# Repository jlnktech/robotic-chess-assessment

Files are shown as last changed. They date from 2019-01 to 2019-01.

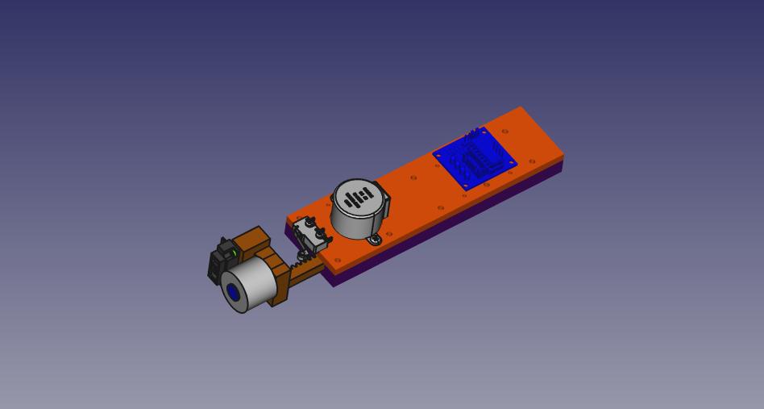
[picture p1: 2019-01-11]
cad/images/image.jpg

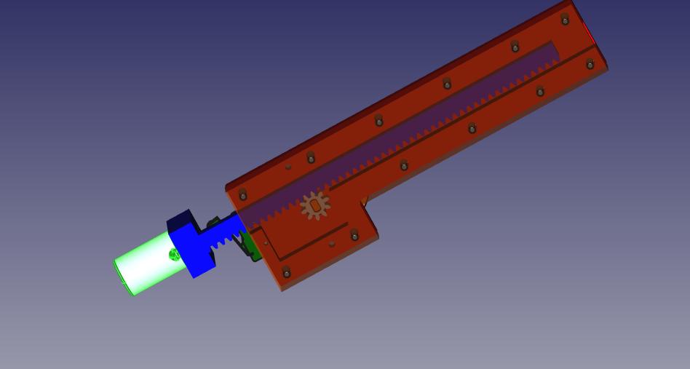
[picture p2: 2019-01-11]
cad/images/image1.jpg

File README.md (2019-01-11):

# robotic-chess-assessment
low cost chess robot

kicad folder contains schematic layout of hall effect detection using DRV5053. Idea is to scan 8 squares (1 row) at once, then repeat for other 7 rows to cut down on time. Each piece must have magnet attached.

pcb123 folder contains schematic layout of IR sensors using QRE1113. Once again, scan 1 row (8 squares) then repeat. Each piece must have reflect material on the bottom and be able to cover the slot on each of the squares.

CAD folder contains the mechanical layout of the xyz table

firmware folder contains arduino test for the z-axis portion

yet to be done is to add the raspberry pi actual chess code

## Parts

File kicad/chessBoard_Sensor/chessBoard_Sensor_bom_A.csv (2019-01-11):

Component | Description | Part | References | Value | Footprint | Quantity Per PCB | Datasheet | Field4 | Category | Status | Family | MPN | Digi-Key_PN | DK_Datasheet_Link | DK_Detail_Page | Manufacturer
1 | 0.1uF ceramic capacitors A capacitor is a passive two-terminal electrical component used to store electrical energy temporarily in an electric field. | 0.1UF-0402-16V-10% | C1 C2 C3 C4 C5 C6 C7 C8 C9 C10 C11 C12 C13 C14 C15 C16 C17 C18 C19 C20 C21 C22 C23 C24 C25 C26 C27 C28 C29 C30 C31 C32 C33 C34 C35 C36 C37 C38 C39 C40 C41 C42 C43 C44 C45 C46 C47 C48 C49 C50 C51 C52 C53 C54 C55 C56 C57 C58 C59 C60 C61 C62 C63 C64 C65 C66 C67 C68 C69 C70 C71 C72 C73 | 0.1UF-0402-16V-10% | 0402 | 73 |  | CAP-12416
2 |  | HEADER_6 | J1 | HEADER_6 | JST_PH_S6B-PH-SM4-TB_1x06-1MP_P2.00mm_Horizontal | 1
3 | Resistor | R | R1 R2 R3 R4 R5 R6 R7 R8 R9 R10 R11 R12 R13 R14 R15 R16 R17 R18 R19 | 10K, 5%, 402 | R_0402_1005Metric | 19 | ~
4 | 3x DIP Switch, Single Pole Single Throw (SPST) switch, small symbol | SW_DIP_x03 | SW1 | SW_DIP_x03 | SW_DIP_SPSTx03_Slide_6.7x9.18mm_W8.61mm_P2.54mm_LowProfile | 1
5 | 12-Bit, 8-Channel, ADC System Monitor With Temperature Sensor, I2C Interface, TSSOP-16 | ADC128D818 | U9 U18 U27 U36 U45 U54 U63 U72 | ADC128D818 | TSSOP-16_4.4x5mm_P0.65mm | 8 | http://www.ti.com/lit/ds/symlink/adc128d818.pdf
6 | SENSOR LINEAR ANALOG SOT23-3 | DRV5053VAQDBZR | U1 U2 U3 U4 U5 U6 U7 U8 U10 U11 U12 U13 U14 U15 U16 U17 U19 U20 U21 U22 U23 U24 U25 U26 U28 U29 U30 U31 U32 U33 U34 U35 U37 U38 U39 U40 U41 U42 U43 U44 U46 U47 U48 U49 U50 U51 U52 U53 U55 U56 U57 U58 U59 U60 U61 U62 U64 U65 U66 U67 U68 U69 U70 U71 | DRV5053VAQDBZR | sot323 | 64 | http://www.ti.com/lit/ds/symlink/drv5053.pdf |  | Sensors, Transducers | Active | Magnetic Sensors - Linear, Compass (ICs) | DRV5053VAQDBZR | 296-38460-1-ND | http://www.ti.com/lit/ds/symlink/drv5053.pdf | /product-detail/en/texas-instruments/DRV5053VAQDBZR/296-38460-1-ND/5022225 | Texas Instruments
7 | 4-channel I2C-bus multiplexer with interrupt logic, TSSOP20 package | PCA9544APW | U73 | PCA9544APW | TSSOP-20_4.4x6.5mm_P0.65mm | 1 | http://www.nxp.com/documents/data_sheet/PCA9544A.pdf
Component Groups: | 7
Component Count: | 167
Fitted Components: | 167
Number of PCBs: | 1
Total components: | 167
Schematic Version: | A
Schematic Date: | 2019-01-01
BoM Date: | Fri 04 Jan 2019 08:12:23 PM PST
Schematic Source: | /home/jlnktech/workspace/kicad_projects/chessBoard_Sensor/chessBoard_Sensor.sch
KiCad Version: | Eeschema 6.0.0-rc1-unknown-62e2fe8~66~ubuntu18.04.1

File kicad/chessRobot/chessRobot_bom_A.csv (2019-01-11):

Component | Description | Part | References | Value | Footprint | Quantity Per PCB | Datasheet | Field4 | Category | Status | Family | MPN | Digi-Key_PN | DK_Datasheet_Link | DK_Detail_Page | Manufacturer
1 | 1uF ceramic capacitors A capacitor is a passive two-terminal electrical component used to store electrical energy temporarily in an electric field. | 1.0UF-0805-25V-10% | C1 | 1.0UF, 25V | 0805 | 1
2 | 47uF polarized capacitors A capacitor is a passive two-terminal electrical component used to store electrical energy temporarily in an electric field. | 47UF-POLAR-EIA3528-10V-10% | C2 C3 | 47UF, 10V | EIA3528 | 2 |  | CAP-08310
3 | 50V 1A General Purpose Rectifier Diode, DO-41 | 1N4001 | D1 D2 | 1N4001 | D_DO-41_SOD81_P10.16mm_Horizontal | 2 | http://www.vishay.com/docs/88503/1n4001.pdf
4 | Generic connector, double row, 02x05, odd/even pin numbering scheme (row 1 odd numbers, row 2 even numbers), script generated (kicad-library-utils/schlib/autogen/connector/) | Conn_02x05_Odd_Even | J1 | 0430201001 |  | 1 | https://www.molex.com/pdm_docs/sd/430201001_sd.pdf
5 | Multi connection point. Often used as Generic Header-pin footprint for 0.1 inch spaced/style header connections <b>On any of the 0.1 inch spaced packages, you can populate with these:</b><ul><li><a href="https://www.sparkfun.com/products/116"> Break Away Headers - Straight</a> (PRT-00116)</li><li><a href="https://www.sparkfun.com/products/553"> Break Away Male Headers - Right Angle</a> (PRT-00553)</li><li><a href="https://www.sparkfun.com/products/115"> Female Headers</a> (PRT-00115)</li><li><a href="https://www.sparkfun.com/products/117"> Break Away Headers - Machine Pin</a> (PRT-00117)</li><li><a href="https://www.sparkfun.com/products/743"> Break Away Female Headers - Swiss Machine Pin</a> (PRT-00743)</li></ul><b> For SCREWTERMINALS and SPRING TERMINALS visit here:</b><ul><li><a href="https://www.sparkfun.com/search/results?term=Screw+Terminals"> Screw Terimnals on SparkFun.com</a> (5mm/3.5mm/2.54mm spacing)</li></ul><b>This device is also useful as a general connection point to wire up your design to another part of your project. Our various solder wires solder well into these plated through hole pads.</b><ul><li><a href="https://www.sparkfun.com/products/11375"> Hook-Up Wire - Assortment (Stranded, 22 AWG)</a> (PRT-11375)</li><li><a href="https://www.sparkfun.com/products/11367"> Hook-Up Wire - Assortment (Solid Core, 22 AWG)</a> (PRT-11367)</li><li><a href="https://www.sparkfun.com/categories/141"> View the entire wire category on our website here</a></li></ul><b>Special notes:</b> Molex polarized connector foot print use with SKU : PRT-08231 with associated crimp pins and housings. 1MM SMD Version SKU: PRT-10208 | CONN_05JST-VERT | J3 | CONN_05JST-VERT | JST-5-PTH-VERT | 1 |  | XXX-00000
6 | Multi connection point. Often used as Generic Header-pin footprint for 0.1 inch spaced/style header connections <b>On any of the 0.1 inch spaced packages, you can populate with these:</b><ul><li><a href="https://www.sparkfun.com/products/116"> Break Away Headers - Straight</a> (PRT-00116)</li><li><a href="https://www.sparkfun.com/products/553"> Break Away Male Headers - Right Angle</a> (PRT-00553)</li><li><a href="https://www.sparkfun.com/products/115"> Female Headers</a> (PRT-00115)</li><li><a href="https://www.sparkfun.com/products/117"> Break Away Headers - Machine Pin</a> (PRT-00117)</li><li><a href="https://www.sparkfun.com/products/743"> Break Away Female Headers - Swiss Machine Pin</a> (PRT-00743)</li></ul><b> For SCREWTERMINALS and SPRING TERMINALS visit here:</b><ul><li><a href="https://www.sparkfun.com/search/results?term=Screw+Terminals"> Screw Terimnals on SparkFun.com</a> (5mm/3.5mm/2.54mm spacing)</li></ul><b>This device is also useful as a general connection point to wire up your design to another part of your project. Our various solder wires solder well into these plated through hole pads.</b><ul><li><a href="https://www.sparkfun.com/products/11375"> Hook-Up Wire - Assortment (Stranded, 22 AWG)</a> (PRT-11375)</li><li><a href="https://www.sparkfun.com/products/11367"> Hook-Up Wire - Assortment (Solid Core, 22 AWG)</a> (PRT-11367)</li><li><a href="https://www.sparkfun.com/categories/141"> View the entire wire category on our website here</a></li></ul><b>Special notes:</b> Molex polarized connector foot print use with SKU : PRT-08231 with associated crimp pins and housings. 1MM SMD Version SKU: PRT-10208 | CONN_05JST-VERT | J2 | JST B5B | B5B-XH-A(LF)(SN) | 1 | http://www.jst-mfg.com/product/pdf/eng/eXH.pdf | XXX-00000
7 | Generic screw terminal, single row, 01x02, script generated (kicad-library-utils/schlib/autogen/connector/) | Screw_Terminal_01x02 | J4 J6 | Screw_Terminal_01x02 |  | 2 | ~
8 | Generic screw terminal, single row, 01x03, script generated (kicad-library-utils/schlib/autogen/connector/) | Screw_Terminal_01x03 | J5 | Screw_Terminal_01x03 |  | 1 | ~
9 | 5-wire unipolar stepper motor | Stepper_Motor_unipolar_5pin | M1 | 858 |  | 1 | https://media.digikey.com/pdf/Data%20Sheets/Adafruit%20PDFs/858_Web.pdf
10 | P-channel MOSFETs Voltage controlled devices that allow control of high current outputs. <b>SparkFun Products:</b><ul><li><a href= https://www.sparkfun.com/products/13907 >SparkFun ESP32 Thing</a></li><li><a href= https://www.sparkfun.com/products/13231 >SparkFun ESP8266 Thing</a></li></ul> | MOSFET_PCH-SI2309DS | Q2 | LR120 | d2-pak | 1
11 | Generic Resistor Package | RESISTOR0603 | R2 | 100, 5% | 0603 | 1
12 | Generic Resistor Package | RESISTOR0603 | R1 | 10K, 5% | 0603 | 1
13 | IC PWR RELAY 7NPN 1:1 16DIP | ULN2003AN | U1 | ULN2003AN | DIP-16_W7.62mm | 1 | http://www.ti.com/lit/ds/symlink/uln2003a.pdf |  | Discrete Semiconductor Products | Active | Transistors - Bipolar (BJT) - Arrays | ULN2003AN | 296-1979-5-ND | http://www.ti.com/lit/ds/symlink/uln2003a.pdf | /product-detail/en/texas-instruments/ULN2003AN/296-1979-5-ND/277624 | Texas Instruments
Component Groups: | 13
Component Count: | 16
Fitted Components: | 16
Number of PCBs: | 1
Total components: | 16
Schematic Version: | A
Schematic Date: | 2019-01-07
BoM Date: | Tue 08 Jan 2019 07:28:10 AM PST
Schematic Source: | /home/jlnktech/workspace/kicad_projects/chessRobot/chessRobot.sch
KiCad Version: | Eeschema 6.0.0-rc1-unknown-62e2fe8~66~ubuntu18.04.1

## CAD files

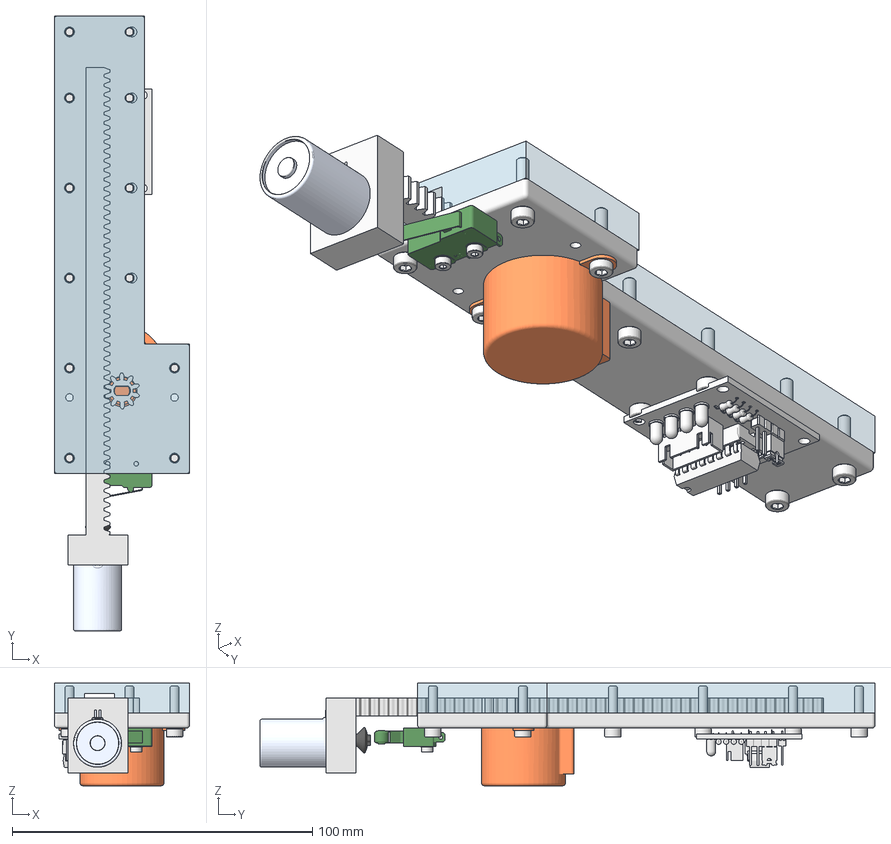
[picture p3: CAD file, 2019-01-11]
cad/assembly.fcstd
45.0 x 204.9 x 34.2 mm
M3x14-Screw002
M3x14-Screw013
M3x14-Screw014
M3x14-Screw016
M3x14-Screw015
M3x14-Screw008
M3x14-Screw009
M3x14-Screw010
M3x14-Screw011
M3x14-Screw012
M3x14-Screw017
M3x14-Screw
M2x10-Screw
M2x10-Screw001
28byj-48
Microswitch
M4x12-Screw
wf-p10-25_electro
basePlate
rack
gear
coverPlate
ULN2003Board

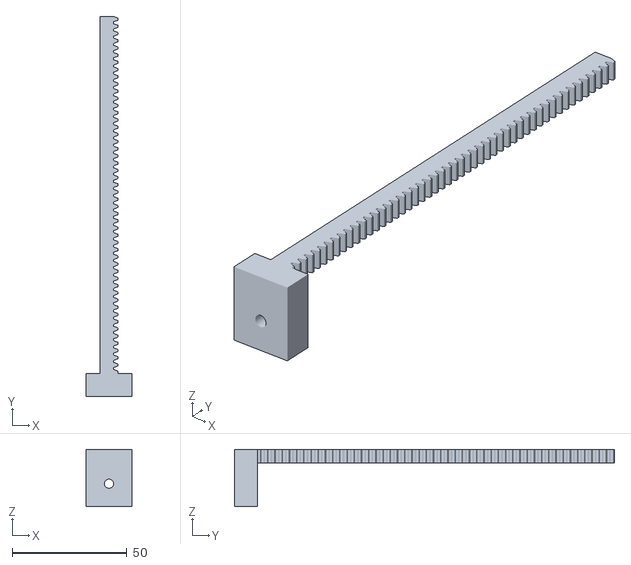
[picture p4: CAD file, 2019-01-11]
cad/3dPrinterFiles/rack.STL
20.0 x 165.7 x 25.0

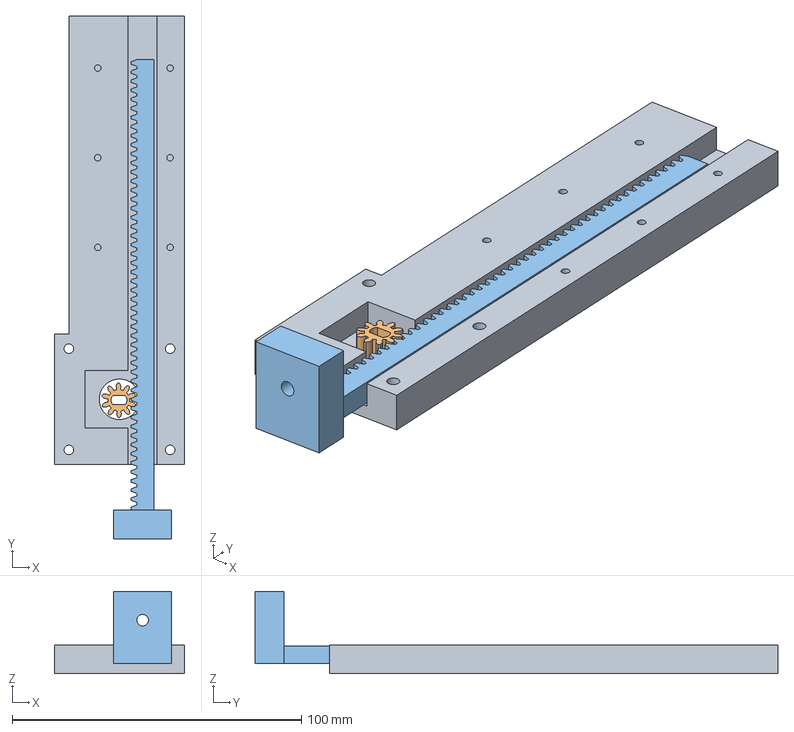
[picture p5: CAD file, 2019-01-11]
cad/new_cover.fcstd
45.0 x 180.8 x 28.5 mm
cover
gear
rack

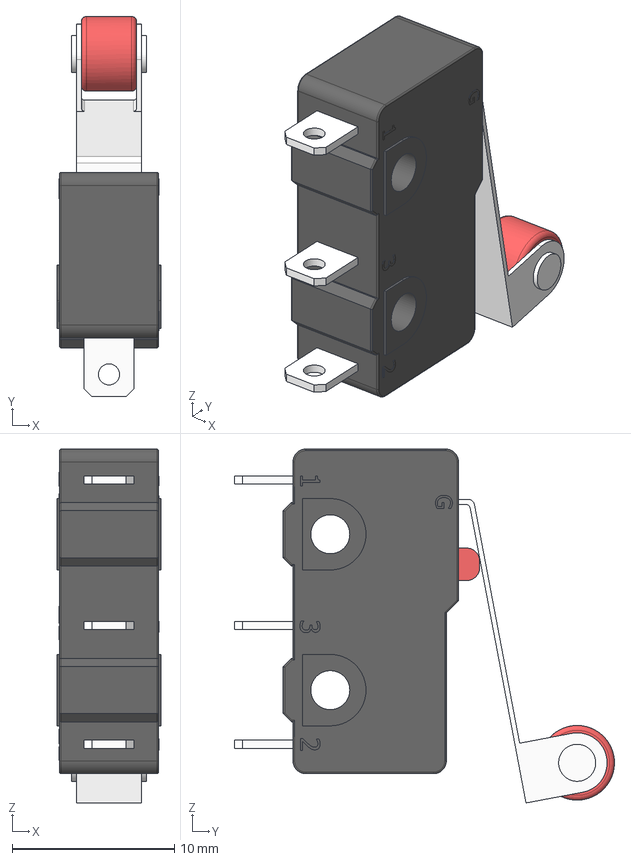
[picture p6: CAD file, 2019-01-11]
cad/support/Microswitch.stp
6.40 x 23.4 x 21.8 mm

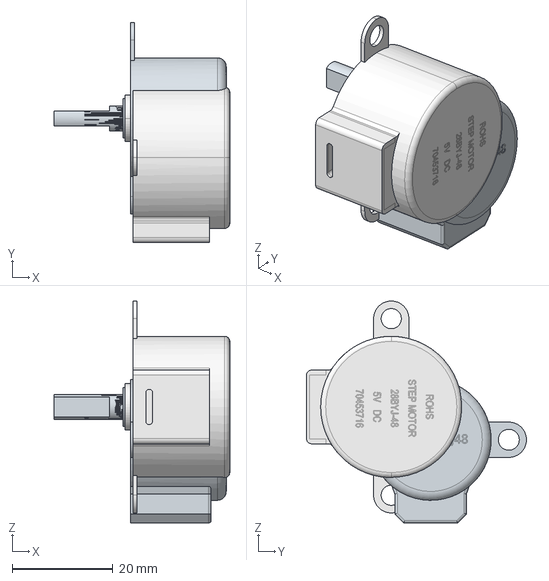
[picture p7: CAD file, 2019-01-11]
cad/tests/motor_combo.fcstd
34.8 x 43.6 x 44.0 mm
5V DC STEP MOTOR

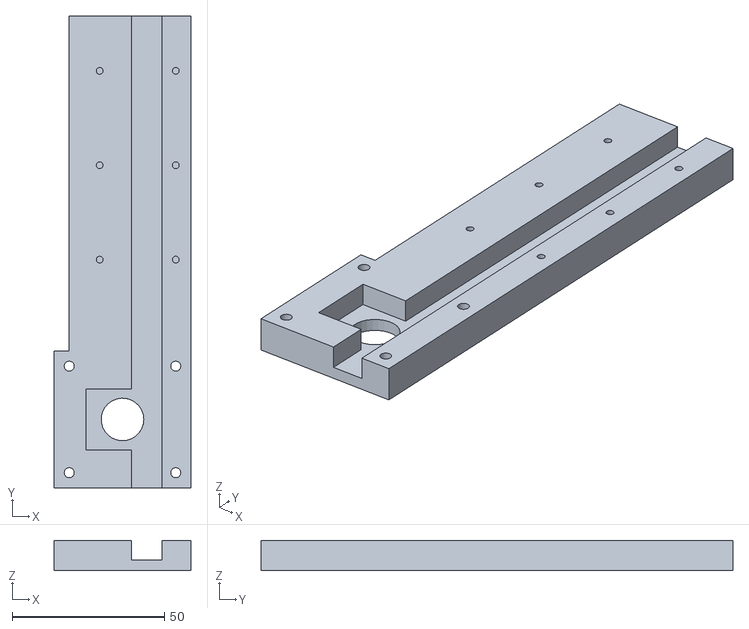
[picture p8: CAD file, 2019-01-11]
cad/3dPrinterFiles/newCover.stl
45.0 x 155.0 x 10.0

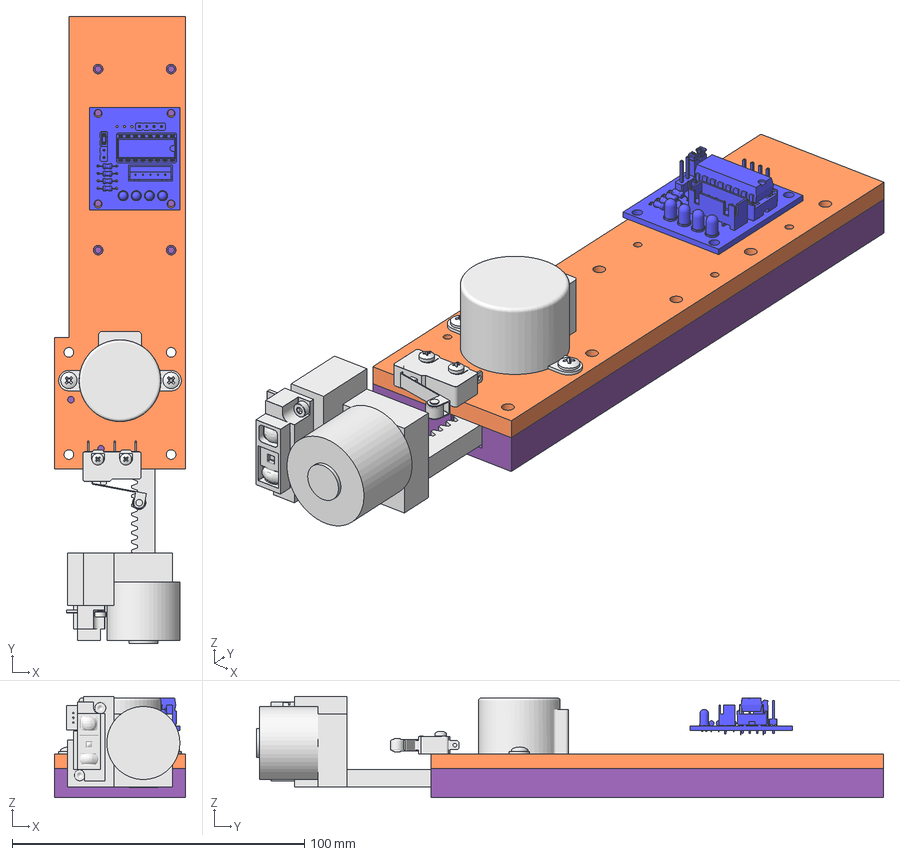
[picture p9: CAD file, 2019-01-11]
cad/new_base_cover.fcstd
45.0 x 214.7 x 34.7 mm
M3x5-Screw
M3x5-Screw001
M2x10-Screw
M2x10-Screw001
Microswitch 20mm
28BYJ-48
newRack
gear
ULN2003Board
newCover
newBase

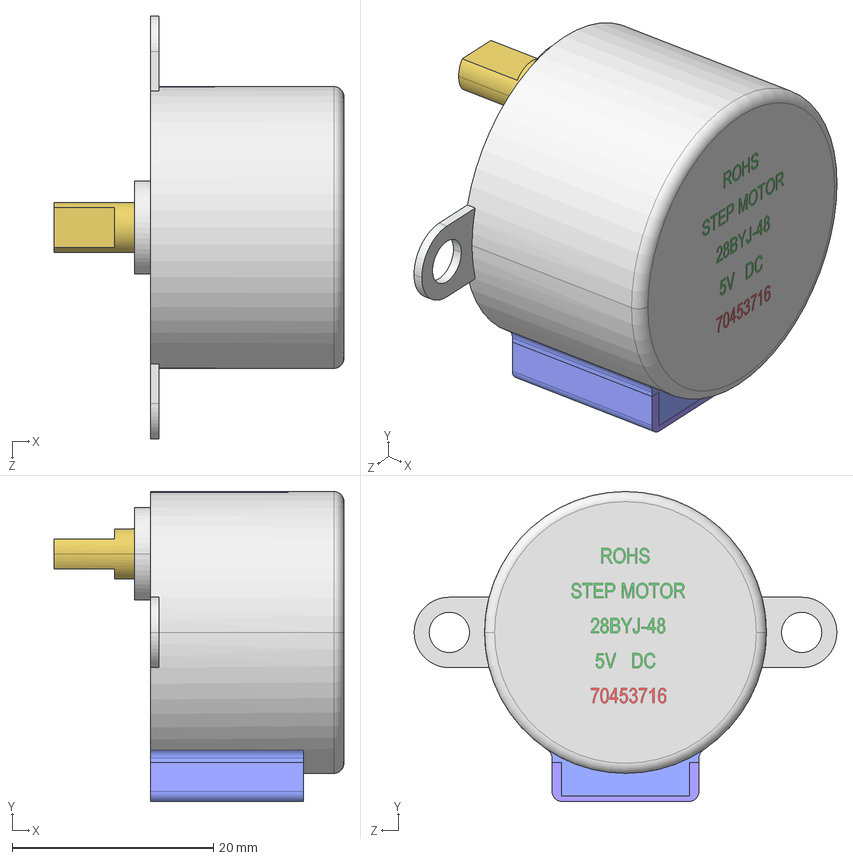
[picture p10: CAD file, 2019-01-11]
cad/support/28byj-48.stp
28.8 x 30.8 x 42.0 mm

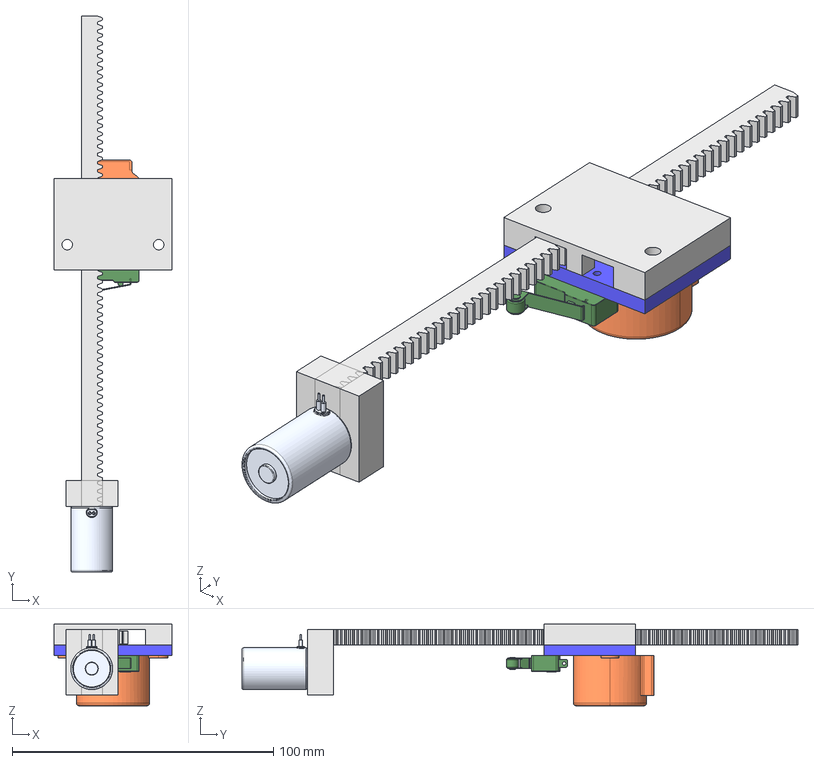
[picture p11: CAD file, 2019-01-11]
cad/tests/stepper_motion_backup.fcstd
45.0 x 212.7 x 31.2 mm
28byj-48
Microswitch 20mm
newGear
wf-p10-25_electro
newRack
newBase
newCover

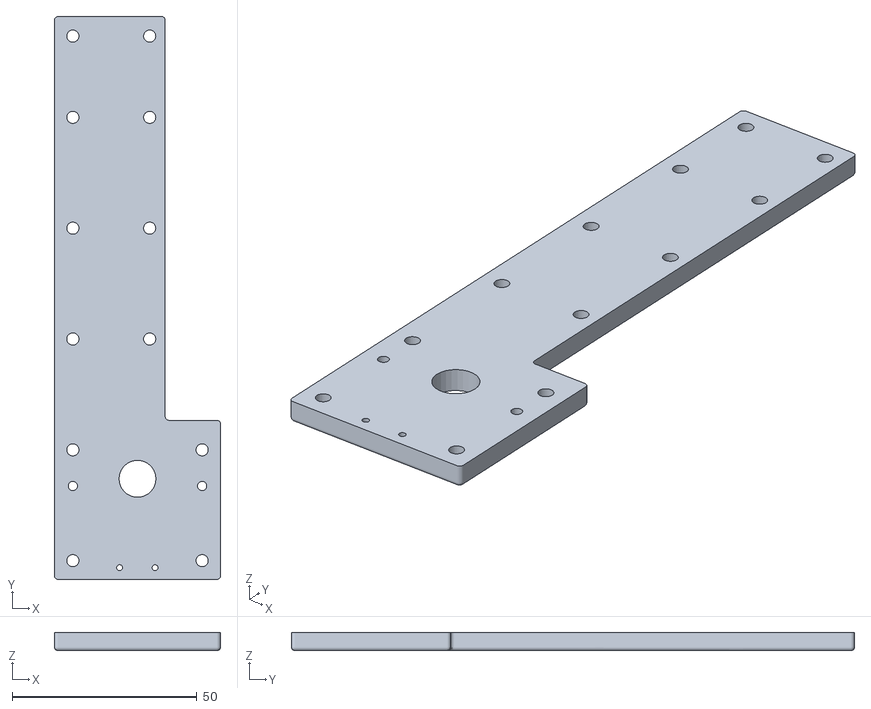
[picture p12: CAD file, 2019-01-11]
cad/3dPrinterFiles/base.stl
45.0 x 152.4 x 5.00

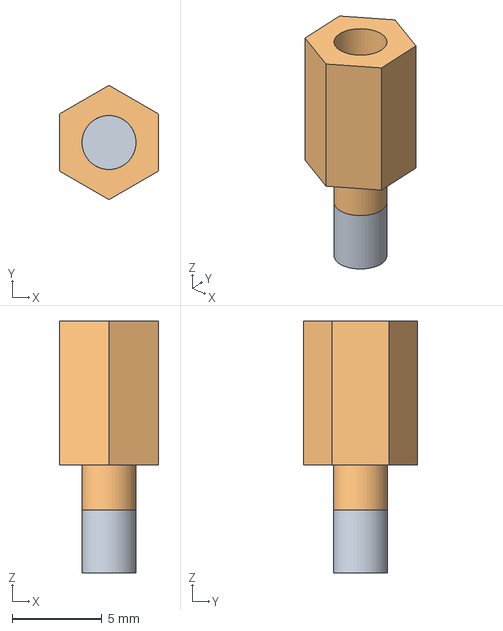
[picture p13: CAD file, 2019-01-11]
cad/support/standoff_m3.fcstd
5.50 x 6.35 x 14.0 mm

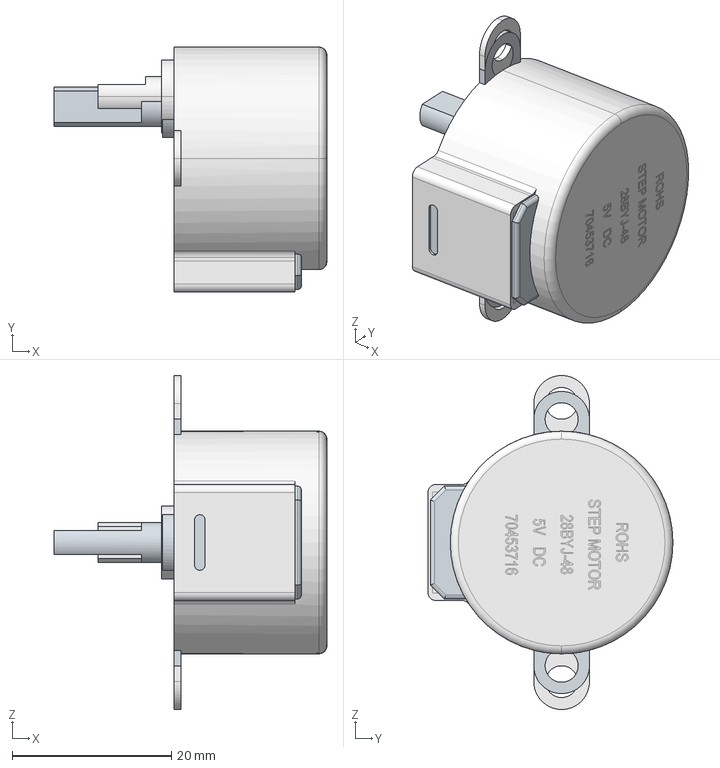
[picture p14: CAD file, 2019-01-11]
cad/tests/measurement_two_motors.fcstd
34.3 x 30.8 x 42.0 mm
28BYJ-48
24BYJ-48

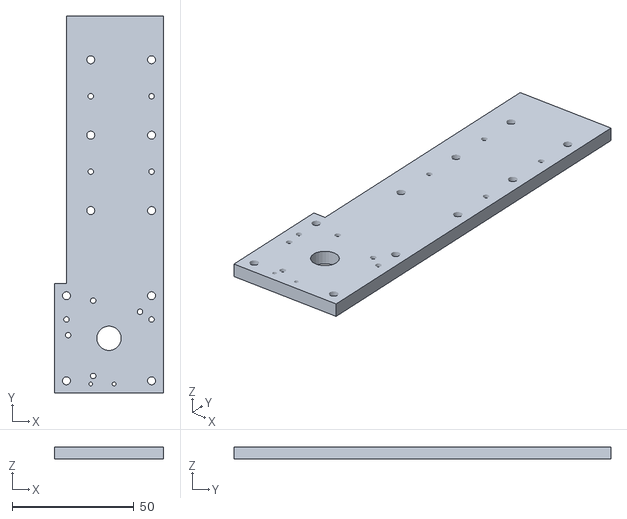
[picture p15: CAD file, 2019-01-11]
cad/3dPrinterFiles/newBase.stl
45.0 x 155.0 x 5.00

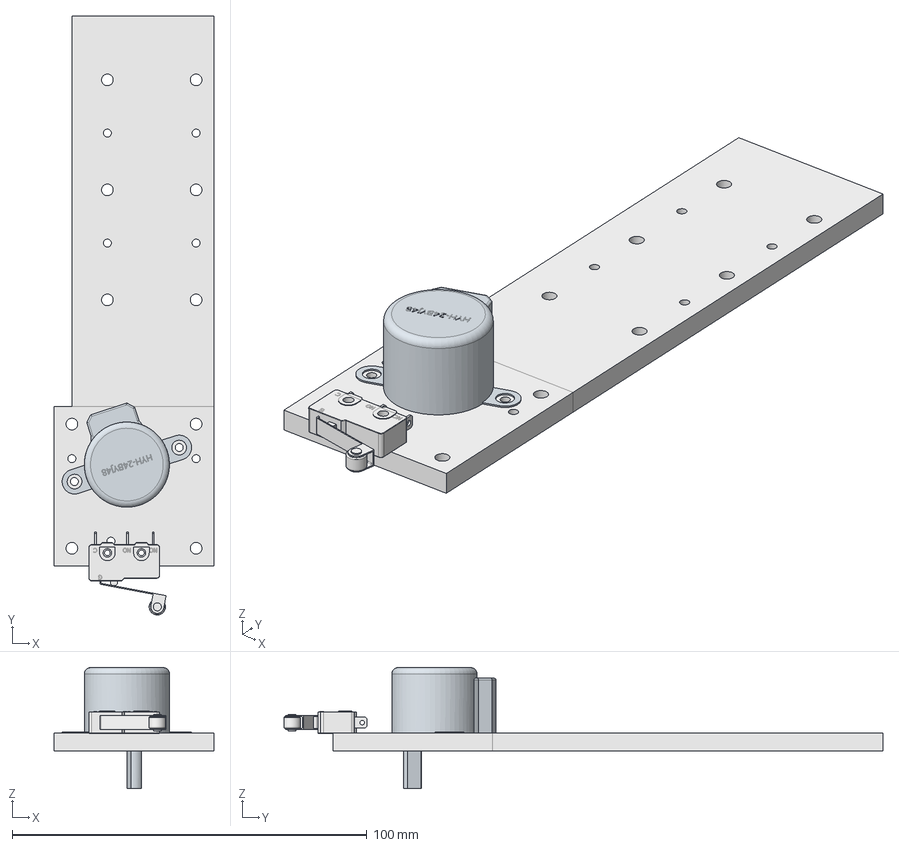
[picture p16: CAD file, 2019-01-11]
cad/new_base.fcstd
45.0 x 168.8 x 34.2 mm
48BYJ-48
Microswitch 20mm
Base

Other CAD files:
cad/support/WF-p25_20.FCStd
cad/tests/stepper_motion.fcstd
cad/3dPrinterFiles/motor_combo.stl
cad/new_rack.FCStd
cad/3dPrinterFiles/cover.stl
cad/3dPrinterFiles/gear.stl
cad/3dPrinterFiles/newRack.stl
cad/old/base.fcstd
cad/old/cover.fcstd
cad/old/gear.fcstd
cad/old/rack.fcstd
cad/support/GP2Y0A51SK0F.FCStd
cad/support/ULN2003Board.stl
cad/support/ULN2003_board.fcstd
cad/support/hyh-24byj48.step
cad/support/sot23-3.fcstd
cad/support/standoff_m3.stl

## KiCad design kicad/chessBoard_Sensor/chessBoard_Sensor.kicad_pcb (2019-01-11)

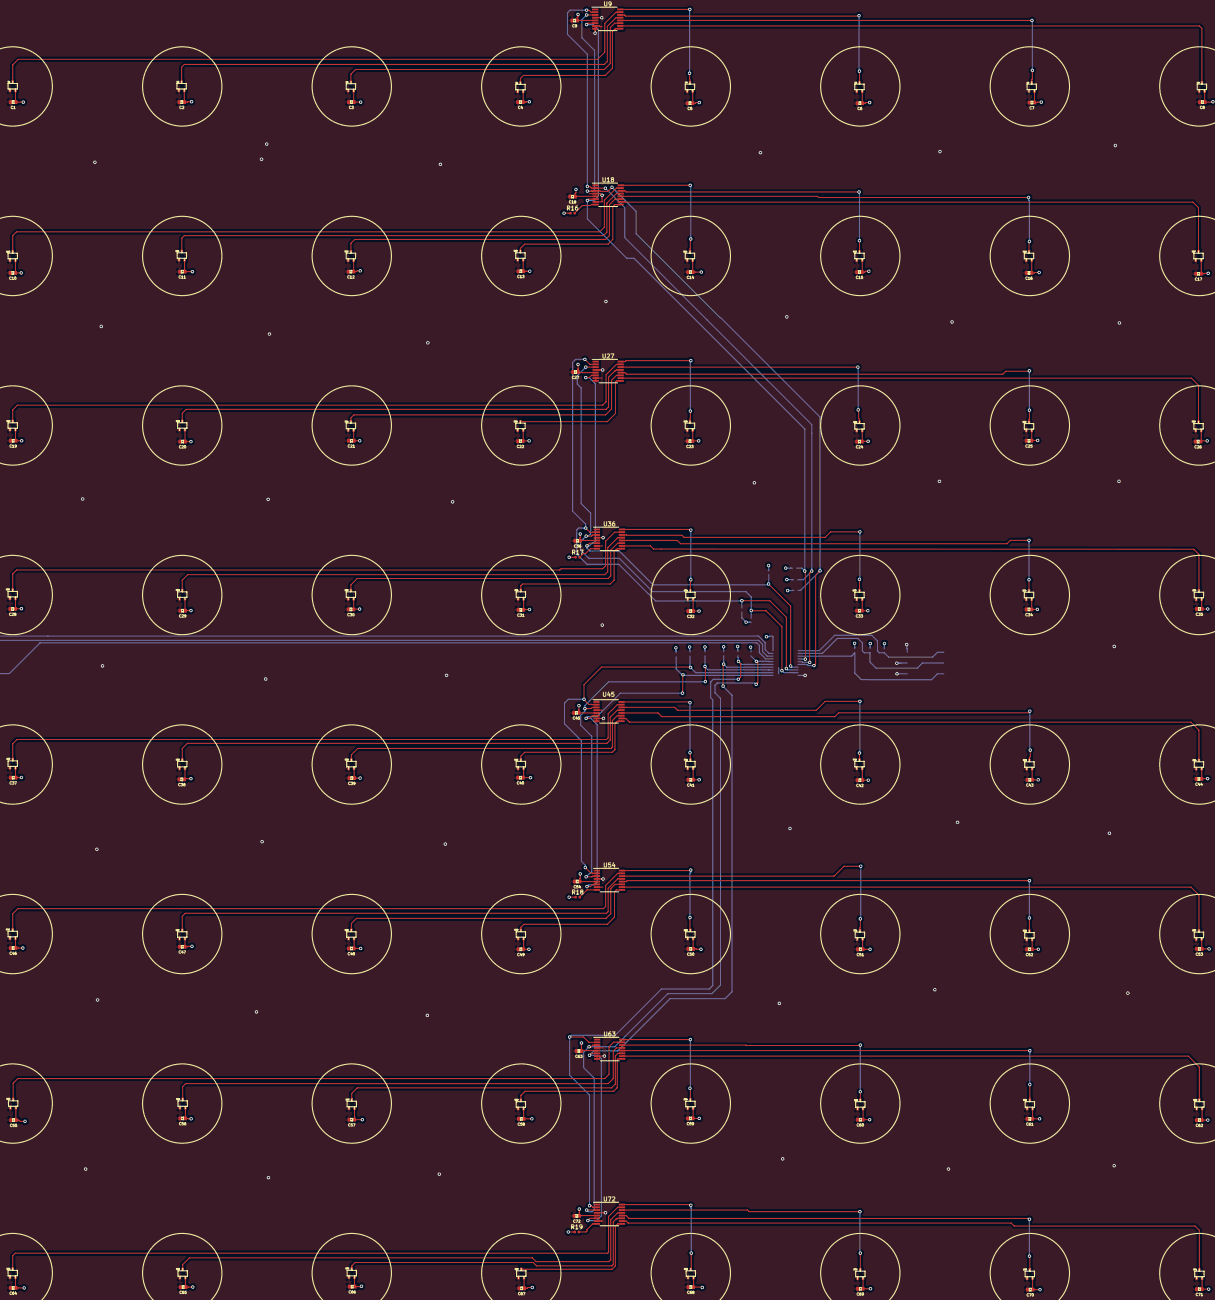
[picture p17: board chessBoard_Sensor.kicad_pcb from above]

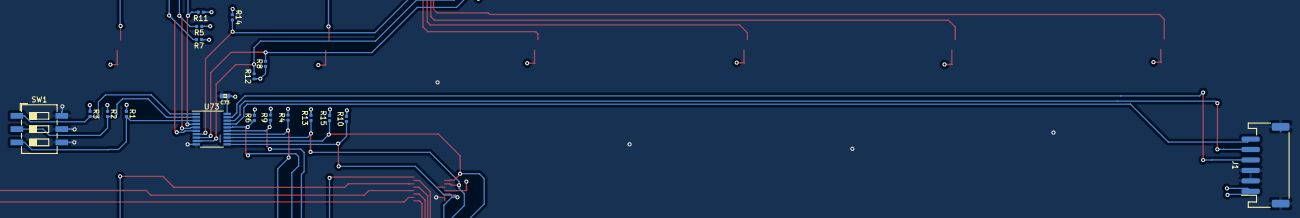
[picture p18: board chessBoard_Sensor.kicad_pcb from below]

Board: 4 copper layers, 167 parts (19 on the bottom side), 88 nets.

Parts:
C1, C2, C3, C4, C5, C6, C7, C8, C9, C10, C11, C12, C13, C14, C15, C16, C17, C18, C19, C20, C21, C22, C23, C24, C25, C26, C27, C28, C29, C30, C31, C32, C33, C34, C35, C36, C37, C38, C39, C40, C41, C42, C43, C44, C45, C46, C47, C48, C49, C50, C51, C52, C53, C54, C55, C56, C57, C58, C59, C60, C61, C62, C63, C64, C65, C66, C67, C68, C69, C70, C71, C72, C73: 0.1UF-0402-16V-10%; 0402
J1: HEADER_6; JST_PH_S6B-PH-SM4-TB_1x06-1MP_P2.00mm_Horizontal
R1, R2, R3, R4, R5, R6, R7, R8, R9, R10, R11, R12, R13, R14, R15, R16, R17, R18, R19: 10K, 5%, 402; R_0402_1005Metric
SW1: SW_DIP_x03; SW_DIP_SPSTx03_Slide_6.7x9.18mm_W8.61mm_P2.54mm_LowProfile
U1, U2, U3, U4, U5, U6, U7, U8, U10, U11, U12, U13, U14, U15, U16, U17, U19, U20, U21, U22, U23, U24, U25, U26, U28, U29, U30, U31, U32, U33, U34, U35, U37, U38, U39, U40, U41, U42, U43, U44, U46, U47, U48, U49, U50, U51, U52, U53, U55, U56, U57, U58, U59, U60, U61, U62, U64, U65, U66, U67, U68, U69, U70, U71: DRV5053VAQDBZR; sot323
U9, U18, U27, U36, U45, U54, U63, U72: ADC128D818; TSSOP-16_4.4x5mm_P0.65mm
U73: PCA9544APW; TSSOP-20_4.4x6.5mm_P0.65mm

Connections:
+3V3: C1.1, C2.1, C3.1, C4.1, C5.1, C6.1, C7.1, C8.1, C9.1, C10.1, C11.1, C12.1, C13.1, C14.1, C15.1, C16.1, C17.1, C18.1, C19.1, C20.1, C21.1, C22.1, C23.1, C24.1, C25.1, C26.1, C27.1, C28.1, C29.1, C30.1, C31.1, C32.1, C33.1, C34.1, C35.1, C36.1, C37.1, C38.1, C39.1, C40.1, C41.1, C42.1, C43.1, C44.1, C45.1, C46.1, C47.1, C48.1, C49.1, C50.1, C51.1, C52.1, C53.1, C54.1, C55.1, C56.1, C57.1, C58.1, C59.1, C60.1, C61.1, C62.1, C63.1, C64.1, C65.1, C66.1, C67.1, C68.1, C69.1, C70.1, C71.1, C72.1, C73.1, J1.1, R1.1, R2.1, R3.1, R4.2, R5.1, R6.2, R7.1, R8.1, R9.2, R10.2, R11.1, R12.1, R13.2, R14.1, R15.2, R16.1, R17.1, R18.1, R19.1, U1.3, U2.3, U3.3, U4.3, U5.3, U6.3, U7.3, U8.3, U9.5, U10.3, U11.3, U12.3, U13.3, U14.3, U15.3, U16.3, U17.3, U18.5, U19.3, U20.3, U21.3, U22.3, U23.3, U24.3, U25.3, U26.3, U27.5, U28.3, U29.3, U30.3, U31.3, U32.3, U33.3, U34.3, U35.3, U36.5, U37.3, U38.3, U39.3, U40.3, U41.3, U42.3, U43.3, U44.3, U45.5, U46.3, U47.3, U48.3, U49.3, U50.3, U51.3, U52.3, U53.3, U54.5, U55.3, U56.3, U57.3, U58.3, U59.3, U60.3, U61.3, U62.3, U63.5, U64.3, U65.3, U66.3, U67.3, U68.3, U69.3, U70.3, U71.3, U72.5, U73.20
/Sheet1/INT1: R11.2, U9.6, U18.6, U73.4
/Sheet1/SCL1: R7.2, U9.3, U18.3, U73.6
/Sheet1/SDA1: R5.2, U9.2, U18.2, U73.5
/sheet5C2B8B4A/INT4: R4.1, U63.6, U72.6, U73.14
/sheet5C2B8B4A/SCL4: R6.1, U63.3, U72.3, U73.16
/sheet5C2B8B4A/SDA4: R9.1, U63.2, U72.2, U73.15
/sheet5C2B89C0/INT3: R10.1, U45.6, U54.6, U73.11
/sheet5C2B89C0/SCL3: R13.1, U45.3, U54.3, U73.13
/sheet5C2B89C0/SDA3: R15.1, U45.2, U54.2, U73.12
/sheet5C2B878C/INT2: R14.2, U27.6, U36.6, U73.7
/sheet5C2B878C/SCL2: R12.2, U27.3, U36.3, U73.9
/sheet5C2B878C/SDA2: R8.2, U27.2, U36.2, U73.8
GND: C1.2, C2.2, C3.2, C4.2, C5.2, C6.2, C7.2, C8.2, C9.2, C10.2, C11.2, C12.2, C13.2, C14.2, C15.2, C16.2, C17.2, C18.2, C19.2, C20.2, C21.2, C22.2, C23.2, C24.2, C25.2, C26.2, C27.2, C28.2, C29.2, C30.2, C31.2, C32.2, C33.2, C34.2, C35.2, C36.2, C37.2, C38.2, C39.2, C40.2, C41.2, C42.2, C43.2, C44.2, C45.2, C46.2, C47.2, C48.2, C49.2, C50.2, C51.2, C52.2, C53.2, C54.2, C55.2, C56.2, C57.2, C58.2, C59.2, C60.2, C61.2, C62.2, C63.2, C64.2, C65.2, C66.2, C67.2, C68.2, C69.2, C70.2, C71.2, C72.2, C73.2, J1.2, J1.3, J1.MP, SW1.4, SW1.5, SW1.6, U1.1, U2.1, U3.1, U4.1, U5.1, U6.1, U7.1, U8.1, U9.4, U9.7, U9.8, U10.1, U11.1, U12.1, U13.1, U14.1, U15.1, U16.1, U17.1, U18.4, U18.7, U19.1, U20.1, U21.1, U22.1, U23.1, U24.1, U25.1, U26.1, U27.4, U27.7, U27.8, U28.1, U29.1, U30.1, U31.1, U32.1, U33.1, U34.1, U35.1, U36.4, U36.7, U37.1, U38.1, U39.1, U40.1, U41.1, U42.1, U43.1, U44.1, U45.4, U45.7, U45.8, U46.1, U47.1, U48.1, U49.1, U50.1, U51.1, U52.1, U53.1, U54.4, U54.7, U55.1, U56.1, U57.1, U58.1, U59.1, U60.1, U61.1, U62.1, U63.4, U63.7, U63.8, U64.1, U65.1, U66.1, U67.1, U68.1, U69.1, U70.1, U71.1, U72.4, U72.7, U73.10
unnamed: J1.4, U73.19
unnamed: J1.5, U73.18
unnamed: J1.6, U73.17
unnamed: R1.2, SW1.3, U73.3
unnamed: R2.2, SW1.2, U73.2
unnamed: R3.2, SW1.1, U73.1
unnamed: R16.2, U18.8
unnamed: R17.2, U36.8
unnamed: R18.2, U54.8
unnamed: R19.2, U72.8
unnamed: U1.2, U9.15
unnamed: U2.2, U9.13
unnamed: U3.2, U9.11
unnamed: U4.2, U9.9
unnamed: U5.2, U9.16
unnamed: U6.2, U9.14
unnamed: U7.2, U9.12
unnamed: U8.2, U9.10
unnamed: U10.2, U18.15
unnamed: U11.2, U18.13
unnamed: U12.2, U18.11
unnamed: U13.2, U18.9
unnamed: U14.2, U18.16
unnamed: U15.2, U18.14
unnamed: U16.2, U18.12
unnamed: U17.2, U18.10
unnamed: U19.2, U27.15
unnamed: U20.2, U27.13
unnamed: U21.2, U27.11
unnamed: U22.2, U27.9
unnamed: U23.2, U27.16
unnamed: U24.2, U27.14
unnamed: U25.2, U27.12
unnamed: U26.2, U27.10
unnamed: U28.2, U36.15
unnamed: U29.2, U36.13
unnamed: U30.2, U36.11
unnamed: U31.2, U36.9
unnamed: U32.2, U36.16
unnamed: U33.2, U36.14
unnamed: U34.2, U36.12
unnamed: U35.2, U36.10
unnamed: U37.2, U45.15
unnamed: U38.2, U45.13
unnamed: U39.2, U45.11
unnamed: U40.2, U45.9
unnamed: U41.2, U45.16
unnamed: U42.2, U45.14
unnamed: U43.2, U45.12
unnamed: U44.2, U45.10
unnamed: U46.2, U54.15
unnamed: U47.2, U54.13
unnamed: U48.2, U54.11
unnamed: U49.2, U54.9
unnamed: U50.2, U54.16
unnamed: U51.2, U54.14
unnamed: U52.2, U54.12
unnamed: U53.2, U54.10
unnamed: U55.2, U63.15
unnamed: U56.2, U63.13
unnamed: U57.2, U63.11
unnamed: U58.2, U63.9
unnamed: U59.2, U63.16
unnamed: U60.2, U63.14
unnamed: U61.2, U63.12
unnamed: U62.2, U63.10
unnamed: U64.2, U72.15
unnamed: U65.2, U72.13
unnamed: U66.2, U72.11
unnamed: U67.2, U72.9
unnamed: U68.2, U72.16
unnamed: U69.2, U72.14
unnamed: U70.2, U72.12
unnamed: U71.2, U72.10

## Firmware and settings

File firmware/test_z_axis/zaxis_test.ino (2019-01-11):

// **********************************************************************************

// Copyright (c) 2018 JLNKTECH Consulting, LLC   All Rights Reserved.
//                    JLNKTECH Consulting, LLC   Proprietary
// ------------------------------------------------------------------------------
// File       : zaxisTest.ino
// Purpose    : test various stepper motors
// Author     : James Garrison
// Started    : 25 December 2018
// Description:
//               D6      electroMagnet

//               D7      limit switch
//               D8      stepper1
//               D9      stepper2
//               D10     stepper3
//               D12     stepper4
//
//               A0      distance sensor
// **********************************************************************************
//
// library cheapStepper has been modified to support homing switch
// during movement up, the limit switch is checked. Default pin 7 uses
// internal pullup and when contacted (logic level low (0)) home has been reached.
// after homing, the software will move away 500 steps.
//
// also added motor off, so that the motor does not overheat. Being geared, don't need to
// worry about movement.
//
// The initial unipolar stepper motor is 28BYJ-48, which has 4096 steps-per-revolution.
// It is an 64:1 ratio geared motor.
//
// Other motors will require adjusting the steps-per-revolution and rpm.
//
//  Motor P/N               Steps/revol       Angle       Ratio       Size (mm)   RPM
//   28BYJ-48                   4096          0.088       64:1         35          15
//  290-028 (24BYJ-48)          1600          5.625       25:1         31         TBD
//  108990003                   2048          0.176       32:1         31         TBD
//     858                       513          0.702       16:1         35          10
//
//
//   sonar using HC-SR04
// **********************************************************************************
// Revision History
// 12-25-18  : Version 1.0 - Initial
//
// 12-28-18  : using UE-1327 12V electro magnet
// 12-28-18  : rpm=15, stepPRv=4096, takes 3300 steps = 1 inch, using 28BYJ-48
// 01-02-19  : rpm=10, stepPRv=513,  takes  800 steps = 1 inch, using 858
// 01-02-19  : rpm=10, stepPRv=1600, takes  xxx steps = 1 inch, using 24BYJ-48-25
//
// 01-04-19  : using WF-P25/50 5V electro magnet
//           : to travel 1 inch, steps = 800, using 858 stepper motor
//           : test setup panel,
//           :      king    pickup at steps=1460
//           :      queen   pickup at steps=1750
//           :      bishop  pickup at steps=2000
//           :      knight  pickup at steps=2100
//           :      rook    pickup at steps=2325
//           :      pawn    pickup at steps=2540
//
// 01-06-19  : add sharp GP2Y0A51SK0F distance sensor for testing
//           : move down about 0.75in and measure object
// **********************************************************************************
#include <Cmd.h>
#include <CheapStepper.h>
#include <EEPROM.h>
#include <TrueRandom.h>
#include <avr/wdt.h>
#include <avr/boot.h>

// distance measurement
#include <SharpDistSensor.h>
#include "Statistic.h"

// default settings
char boardName[32]        = "chessRobot";      // do not change
const long magicNumber    = 0x67FB;            // magic number;
char firmwareVersion[10]  = "1.0.0";           // firmware, change as changes are made and release
char boardVersion[10]     = "A/A";             // changes only when board is changed ( board revision / schematic revision )
char boardDate[11]        = "12/25/2018";      // date of last change
char boardSerial[7]       = "000000";          // default, do not change

// board UUID address
// auto generated on-board
byte uuid[16] = {
  0, 0, 0, 0, 0, 0, 0, 0, 0, 0, 0, 0, 0, 0, 0, 0
};

// eeprom address locations for factory data
const int addr_serial   = 0;
const int addr_bversion = 10;
const int addr_fversion = 20;
const int addr_date     = 40;
const int addr_mac      = 60;
const int addr_uuid     = 90;

// eeprom size ( ATMega328P )
const int EEPROM_MIN_ADDR = 0;
const int EEPROM_MAX_ADDR = 1023;

//             (sensePin, in1, in2, in3, in4)
CheapStepper stepper(7, 8, 9, 10, 12);

// electro magnet switch
#define electroMag 6

boolean dirUp   = true;
boolean dirDown = false;

//int stepsPerRev = 4096;  // 28BYI-48
//int rpm         = 15;

int stepsPerRev = 513;     // 858
int rpm         = 10;

//int stepsPerRev = 2048;     // 108990003
//int rpm         = 10;

//int stepsPerRev = 64;  // 24BYJ-48
//int rpm         = 10;

// distance sensor
#define sensorPin A0

// Window size of the median filter (odd number, 1 = no filtering)
const byte medianFilterWindowSize = 5;

// Create an object instance of the SharpDistSensor class
SharpDistSensor sensor(sensorPin, medianFilterWindowSize);

Statistic stats;
//
// --------------------------------------- Bootloader ------------------------------------------------------------------------
//
// *** Jumping To The Bootloader ***
//
// Shutting Off Peripherals and Interrupts
// Before jumping to the bootloader, you MUST completely disable all interrupt sources and any peripherals you have activated.
// If the watchdog timer has been activated, it must be turned off.
//
// The USB must be disabled. When the UDCON register is written to 1, the attach resistor which signals the presence of a USB device
// is disconnected. Within 5 ms, the PC should recognize that no device is connected (even though the cable is still plugged in). A 5
// ms delay is advisable after disabling the USB. When the bootloader begins, it will enable and reconnect the USB, so it is importan

// to give the PC time to recognize the disconnect.
void enableBootLoader()
{
  cli();
  // disable watchdog, if enabled
  // disable all peripherals

  // UDCON = 1;
  // USBCON = (1<<FRZCLK);  // disable USB
  // UCSR1B = 0;

  _delay_ms(5);

  EIMSK  = 0;
  PCICR  = 0;
  SPCR   = 0;
  ACSR   = 0;
  EECR   = 0;
  ADCSRA = 0;
  TIMSK0 = 0;
  TIMSK1 = 0;
  TIMSK2 = 0;
  // TIMSK3 = 0;
  // UCSR1B = 0;
  TWCR   = 0;
  //  DDRA   = 0;
  DDRB   = 0;
  DDRC   = 0;
  DDRD   = 0;
  //  DDRE   = 0;
  //  DDRF   = 0;
  //  PORTA  = 0;
  PORTB  = 0;
  PORTC  = 0;
  PORTD  = 0;
  //  PORTE  = 0;
  //  PORTF  = 0;

  asm volatile("jmp 0x1E000");
}

// software reset
void restartCode()
{
  Serial.println("Rebooting...");
  delay(500);

  cli();
  wdt_disable();

  EIMSK  = 0;
  PCICR  = 0;
  SPCR   = 0;
  ACSR   = 0;
  EECR   = 0;
  ADCSRA = 0;
  TIMSK0 = 0;
  TIMSK1 = 0;
  TIMSK2 = 0;
  //  TIMSK3 = 0;
  //  UCSR1B = 0;
  TWCR   = 0;
  //  DDRA   = 0;
  DDRB   = 0;
  DDRC   = 0;
  DDRD   = 0;
  //  DDRE   = 0;
  //  DDRF   = 0;
  //  PORTA  = 0;
  PORTB  = 0;
  PORTC  = 0;
  PORTD  = 0;
  //  PORTE  = 0;
  //  PORTF  = 0;

  void(* resetFunc) (void) = 0; //declare reset function @ address 0
  resetFunc();  //call reset

  while (1)
    delay(1000);
}

//
//==========================EEProm Section=====================================
//
// erase eeprom
void eepromEraseAll()
{
  byte b = 0xFF;
  int i;

  for ( i = 0; i <= EEPROM_MAX_ADDR; i++ ) {
    eeprom_write_byte( (unsigned char *) i, b );
  }
}

// Returns true if the address is between the
// minimum and maximum allowed values,
// false otherwise.
//
// This function is used by the other, higher-level functions
// to prevent bugs and runtime errors due to invalid addresses.
boolean eeprom_is_addr_ok( int addr )
{
  return ( ( addr >= EEPROM_MIN_ADDR ) && (addr <= EEPROM_MAX_ADDR) );
}

// Writes a sequence of bytes to eeprom starting at the specified address.
// Returns true if the whole array is successfully written.
// Returns false if the start or end addresses aren't between
// the minimum and maximum allowed values.
boolean eeprom_writeBytes( int startAddr, const byte* array, int numBytes )
{
  // counter
  int i;

  // both first byte and last byte addresses must fall within
  // the allowed range
  if ( !eeprom_is_addr_ok(startAddr) || !eeprom_is_addr_ok(startAddr + numBytes) ) {
    return false;
  }

  for ( i = 0; i < numBytes; i++ ) {
    eeprom_write_byte( (unsigned char *) startAddr + i, array[i] );
  }

  return true;
}

// Reads the specified number of bytes from the specified address into the provided buffer.
// Returns true if all the bytes are successfully read.
// Returns false if the star or end addresses aren't between
// the minimum and maximum allowed values.
// When returning false, the provided array is untouched.
//
// Note: the caller must ensure that array[] has enough space
// to store at most numBytes bytes.
boolean eeprom_readBytes( int startAddr, byte array[], int numBytes )
{
  int i;

  // both first byte and last byte addresses must fall within
  // the allowed range
  if ( !eeprom_is_addr_ok( startAddr ) || !eeprom_is_addr_ok( startAddr + numBytes ) ) {
    return false;
  }

  for ( i = 0; i < numBytes; i++ ) {
    array[i] = eeprom_read_byte( (unsigned char *) startAddr + i );
  }

  return true;
}

// Writes an int variable at the specified address.
// Returns true if the variable value is successfully written.
// Returns false if the specified address is outside the
// allowed range or too close to the maximum value
// to store all of the bytes (an int variable requires
// more than one byte).
boolean eeprom_writeInt( int addr, int value )
{
  byte *ptr;

  ptr = ( byte* )&value;
  return eeprom_writeBytes( addr, ptr, sizeof( value ) );
}

// Reads an integer value at the specified address.
// Returns true if the variable is successfully read.
// Returns false if the specified address is outside the
// allowed range or too close to the maximum vlaue
// to hold all of the bytes (an int variable requires
// more than one byte).
//
boolean eeprom_readInt( int addr, int* value )
{
  return eeprom_readBytes( addr, ( byte* )value, sizeof( int ) );
}

// Writes a string starting at the specified address.
// Returns true if the whole string is successfully written.
// Returns false if the address of one or more bytes
// fall outside the allowed range.
// If false is returned, nothing gets written to the eeprom.
boolean eeprom_writeString( int addr, const char* string )
{
  // actual number of bytes to be written
  int numBytes;

  // we'll need to write the string contents
  // plus the string terminator byte (0x00)
  numBytes = strlen( string ) + 1;

  return eeprom_writeBytes( addr, ( const byte* )string, numBytes );
}

// Reads a string starting from the specified address.
// Returns true if at least one byte (even only the
// string terminator one) is read.
// Returns false if the start address falls outside
// or declare buffer size is zero.
// the allowed range.
// The reading might stop for several reasons:
// - no more space in the provided buffer
// - last eeprom address reached
// - string terminator byte (0x00) encountered.
// The last condition is what should normally occur.
boolean eeprom_readString( int addr, char* buffer, int bufSize )
{
  // byte read from eeprom
  byte ch;

  // number of bytes read so far
  int bytesRead;

  // check start address
  if ( !eeprom_is_addr_ok( addr ) ) {
    return false;
  }

  // how can we store bytes in an empty buffer ?
  if ( bufSize == 0 ) {
    return false;
  }

  // is there is room for the string terminator only,
  // no reason to go further
  if ( bufSize == 1 ) {
    buffer[0] = 0;
    return true;
  }

  // initialize byte counter
  bytesRead = 0;

  // read next byte from eeprom
  ch = eeprom_read_byte( (unsigned char *) addr + bytesRead );

  // store it into the user buffer
  buffer[bytesRead] = ch;

  // increment byte counter
  bytesRead++;

  // stop conditions:
  // - the character just read is the string terminator one (0x00)
  // - we have filled the user buffer
  // - we have reached the last eeprom address
  while ( ( ch != 0x00 ) && ( bytesRead < bufSize ) && ( ( addr + bytesRead ) <= EEPROM_MAX_ADDR ) ) {
    // if no stop condition is met, read the next byte from eeprom
    ch = eeprom_read_byte( (unsigned char *) addr + bytesRead );

    // store it into the user buffer
    buffer[bytesRead] = ch;

    // increment byte counter
    bytesRead++;
  }

  // make sure the user buffer has a string terminator
  // (0x00) as its last byte
  if ( ( ch != 0x00 ) && ( bytesRead >= 1 ) ) {
    buffer[bytesRead - 1] = 0;
  }

  return true;
}

// Dump eeprom memory contents over serial port in tabular form.
// Each printed row shows the value of bytesPerRow bytes
void eepromSerialDumpTable()
{
  int bytesPerRow = 16;
  int i;
  int j;
  byte b;
  static char buf[10];

  // initialize row counter
  j = 0;

  // go from first to last eeprom address
  for ( i = 0; i <= EEPROM_MAX_ADDR; i++ ) {

    // if this is the first byte of the row,
    // start row by printing the byte address
    if ( j == 0 ) {
      sprintf( buf, "%03X: ", i );
      // serial
      Serial.print( buf );
    }

    // read current byte from eeprom
    b = eeprom_read_byte((unsigned char *) i);

    // write byte in hex form
    sprintf( buf, "%02X ", b );

    // increment row counter
    j++;

    // if this is the last byte of the row,
    // reset row counter and use println()
    // to start a new line
    if ( j == bytesPerRow ) {
      j = 0;

      // serial
      Serial.println( buf );
    }
    // else just print the hex value with print()
    else {
      // serial
      Serial.print( buf );
    }
  }

  returnResponse();
}

// read magicNumber, requires 2 bytes (long)
// lets us know that the board is configured
long readMagic()
{
  byte hiByte;
  byte loByte;

  hiByte = EEPROM.read( 4090 );
  loByte = EEPROM.read( 4091 );
  return ( hiByte << 8 ) + loByte;
}

// write magicNumber, uses 2 bytes (long)
// use for configuration setup
void writeMagic()
{
  byte hiByte;
  byte loByte;

  loByte = byte( magicNumber );
  hiByte = byte( magicNumber >> 8 );

  EEPROM.write( 4090, hiByte );
  EEPROM.write( 4091, loByte );
}

// read integer value
int eeReadInt(int address)
{
  return ( EEPROM.read( address) << 8 ) + EEPROM.read( address + 1 );
}

// write integer value
void eeWriteInt(int address, int value)
{
  EEPROM.write( address, (byte) (value >> 8) & 0xFF);
  EEPROM.write( address + 1, (byte) value & 0xFF );
}

//
//==========================Board Info Section=====================================
//
// factory default settings
void setFactoryDefaultSettings()
{
  static char buf[10];

  // board date
  Serial.println( F( "Writing date..." ) );
  eeprom_writeString( addr_date, boardDate );

  // board serial
  Serial.println( F( "Writing serial..." ) );
  eeprom_writeString( addr_serial, boardSerial );

  // firmware version
  Serial.println( F( "Writing firmware version..." ) );
  eeprom_writeString( addr_fversion, firmwareVersion );

  // board version
  Serial.println( F( "Writing board version..." ) );
  eeprom_writeString( addr_bversion, boardVersion );

  returnResponse();
}

// set factory settings
void setFactorySettings( int arg_cnt, char **args )
{
  int strNum;

  // board date
  if ( strcmp( args[2], "date" ) == 0 ) {
    eeprom_writeString( addr_date, args[3] );
  }

  // board serial
  if ( strcmp( args[2], "serial" ) == 0 ) {
    eeprom_writeString( addr_serial, args[3] );
  }

  // board version
  if ( strcmp( args[2], "boardVersion" ) == 0 ) {
    eeprom_writeString( addr_bversion, args[3] );
  }

  // firmware version
  if ( strcmp( args[2], "firmwareVersion" ) == 0 ) {
    eeprom_writeString( addr_fversion, args[3] );
  }

  // board uuid address
  if ( strcmp( args[2], "uuidAddress" ) == 0 ) {
    uuid[0] = cmdStr2Num( args[3], 10 );
    uuid[1] = cmdStr2Num( args[4], 10 );
    uuid[2] = cmdStr2Num( args[5], 10 );
    uuid[3] = cmdStr2Num( args[6], 10 );
    uuid[4] = cmdStr2Num( args[7], 10 );
    uuid[5] = cmdStr2Num( args[8], 10 );
    uuid[6] = cmdStr2Num( args[9], 10 );
    uuid[7] = cmdStr2Num( args[10], 10 );
    uuid[8] = cmdStr2Num( args[11], 10 );
    uuid[9] = cmdStr2Num( args[12], 10 );
    uuid[10] = cmdStr2Num( args[13], 10 );
    uuid[11] = cmdStr2Num( args[14], 10 );
    uuid[12] = cmdStr2Num( args[15], 10 );
    uuid[13] = cmdStr2Num( args[16], 10 );
    uuid[14] = cmdStr2Num( args[17], 10 );
    uuid[15] = cmdStr2Num( args[18], 10 );
    eeprom_writeBytes(addr_uuid, uuid, 16);
  }

  returnResponse();
}

// get factory settings
void getFactorySettings()
{
  // board date
  eeprom_readString( addr_date, boardDate, sizeof( boardDate ) );

  // board serial
  eeprom_readString( addr_serial, boardSerial, sizeof( boardSerial ) );

  // firmware version
  eeprom_readString( addr_fversion, firmwareVersion, sizeof( firmwareVersion ) );

  // board version
  eeprom_readString( addr_bversion, boardVersion, sizeof( boardVersion ) );

  // board uuid address
  eeprom_readBytes(addr_uuid, uuid, 16);
}

//
//==========================Routines Section=====================================
void returnResponse()
{
  // serial
  Serial.println(F("ok"));
}

// Helper function for free ram.
int freeRam()
{
  extern unsigned int __heap_start;
  extern void *__brkval;

  int free_memory;
  int stack_here;

  if (__brkval == 0)
    free_memory = (int) &stack_here - (int) &__heap_start;
  else
    free_memory = (int) &stack_here - (int) __brkval;

  return (free_memory);
}

// return the configuration
void displayMessage()
{
  Serial.print(boardName);
  Serial.print(F(" "));
  Serial.print(boardVersion);
  Serial.print(F(" ("));
  Serial.print( firmwareVersion );
  Serial.print(F(")  ("));
  Serial.print(boardDate);
  Serial.println(F(")"));

  returnResponse();
}

// display date
void printFSDate()
{
  Serial.println(boardDate);
  returnResponse();
}

// print out the factory settings
void printFSBoardVersion()
{
  Serial.println(boardVersion);
  returnResponse();
}

// print out the factory settings
void printFSFirmwareVersion()
{
  Serial.println(firmwareVersion);
  returnResponse();
}

// display name
void printFSBoardName()
{
  Serial.println(boardName);
  returnResponse();
}

// display serial
void printFSSerial()
{
  Serial.println(boardSerial);
  returnResponse();
}

// pretty print out the free ram
void AvailableRAM(int arg_cnt, char **args)
{
  Serial.print(F("Available RAM is "));
  Serial.println(freeRam());

  returnResponse();
}

// pretty print
void printHex(byte number)
{
  int topDigit = number >> 4;
  int bottomDigit = number & 0x0f;

  // Print high hex digit
  Serial.print("0123456789ABCDEF"[topDigit]);
  // Low hex digit
  Serial.print("0123456789ABCDEF"[bottomDigit]);
}

// print out the UUID
void printUUID()
{
  int i;
  for ( i = 0; i < 16; i++ ) {
    if ( i == 4 ) Serial.print(F("-"));
    if ( i == 6 ) Serial.print(F("-"));
    if ( i == 8 ) Serial.print(F("-"));
    if ( i == 10 ) Serial.print(F("-"));

    printHex(uuid[i]);
  }

  Serial.println(F(""));
  returnResponse();
}

// internally generate uuid address
void genUUIDAddress()
{
  Serial.println(F("Generating random numbers..."));
  TrueRandom.uuid( uuid );
  Serial.print( F("uuid Address is "));
  printUUID();
  Serial.println( F("Writing uuid..."));
  eeprom_writeBytes(addr_uuid, uuid, 16);

  returnResponse();
}

// display version
void versionDisplay(int arg_cnt, char **args)
{
  displayMessage();
}

// system commands
void sysCommand(int arg_cnt, char **args)
{
  if (arg_cnt > 1) {
    // commands
    if ( strcmp( args[1], "setFS" ) == 0 ) {
      setFactorySettings( arg_cnt, args );
    } else if ( strcmp( args[1], "genUUID" ) == 0 ) {
      genUUIDAddress();
    } else if ( strcmp( args[1], "setFDS" ) == 0 ) {
      setFactoryDefaultSettings();
    } else if ( strcmp( args[1], "refreshFS" ) == 0 ) {
      getFactorySettings();
    } else if ( strcmp( args[1], "getFSUUID" ) == 0 ) {
      printUUID();
    } else if ( strcmp( args[1], "getFSSerial" ) == 0 ) {
      printFSSerial();
    } else if ( strcmp( args[1], "getFSBoardName" ) == 0 ) {
      printFSBoardName();
    } else if ( strcmp( args[1], "getFSBoardVersion" ) == 0 ) {
      printFSBoardVersion();
    } else if ( strcmp( args[1], "getFSFirmwareVersion" ) == 0 ) {
      printFSFirmwareVersion();
    } else if ( strcmp( args[1], "getFSDate" ) == 0 ) {
      printFSDate();
    } else if ( strcmp( args[1], "eraseEE" ) == 0 ) {
      eepromEraseAll();
    } else if ( strcmp( args[1], "writeMagNum" ) == 0 ) {
      writeMagic();
    } else if ( strcmp( args[1], "dumpEE" ) == 0 ) {
      eepromSerialDumpTable();
    } else {
      Serial.println(F("Unknown command given"));
    }
  } else {
    Serial.println(F("Unknown sys command given"));
  }
}

//
//==========================Stepper Motion Section=====================================
//
// return home
void homePos(int arg_cnt, char **args)
{
  int steps = 20000;

  stepper.move(dirUp, steps);
}

// turn motor off
void motorOff(int arg_cnt, char **args)
{
  stepper.motorOff();
}

// move up by x steps
void moveUp(int arg_cnt, char **args)
{
  int steps;

  if (arg_cnt > 1) {
    steps = cmdStr2Num(args[1], 10);
  } else {
    Serial.println(F("Please provide proper steps"));
    Serial.print(F("from 0 to "));
    Serial.print(stepsPerRev);
    Serial.println(F(")"));
    return;
  }

  stepper.move(dirUp, steps);
}

// move down by x steps
void moveDown(int arg_cnt, char **args)
{
  int steps;

  if (arg_cnt > 1) {
    steps = cmdStr2Num(args[1], 10);
  } else {
    Serial.println(F("Please provide proper steps"));
    Serial.print(F("from 0 to "));
    Serial.print(stepsPerRev);
    Serial.println(F(")"));
    return;
  }

  stepper.move(dirDown, steps);
}

// move up by x steps, tracking steps
void moveToUp(int arg_cnt, char **args)
{
  int steps;

  if (arg_cnt > 1) {
    steps = cmdStr2Num(args[1], 10);
  } else {
    Serial.println(F("Please provide proper steps"));
    Serial.print(F("from 0 to "));
    Serial.print(stepsPerRev);
    Serial.println(F(")"));
    return;
  }

  stepper.moveTo(dirUp, steps);
}
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
void loop()
{
  cmdPoll();
}
